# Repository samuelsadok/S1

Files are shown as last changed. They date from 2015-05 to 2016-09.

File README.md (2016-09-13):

# AppInstall Innovation Labs S1

The S1 project is a small pocket drone, controlled by your smartphone via Bluetooth.

## Project State

Until now, about 10 instances of a prototype were manufactured. The firmware was written to a point where the throttle could be controlled by an iOS App. However, since then, the PID-controller has never been properly tuned, so flight could not yet be demonstrated.

To allow for better understanding of the physical system, and ultimately enable autonomous controller calibration, the implementation of a software-in-the-loop simulator was started.

The desire to make the contol protocol and application more universal contributed to the inception of the AmbientOS project. Since then, no progress was made on the S1 project. It will be resumed once the AmbientOS framework is capable enough to carry the S1 control App.

## Hardware Overview

The most important hardware components on the S1 prototype 1 hardware are:
- an AVR ATXmega32E5 microcontroller, dedicated to flight control tasks ("flight controller")
- a CSR1010 bluetooth microcontroller, dedicated to bluetooth communication ("baseband processor")
- an InvenSense MPU6050 inertial sensor (connected to the flight controller)
- 4 MOSFETs used to control the motors (connected to the flight controller)

The two microcontrollers are connected through an I2C connection, where the baseband processor
is the master and the flight controller is the slave.

## Known Hardware Issues

Hardware bugs in the S1 prototype 1 hardware, to be solved in updated versions:

 - the power supply is not stable when the motors draw a lot of current (possibly solved using a large (330 µF) capacitor)
 - the motor drivers require a capacitor and a resistor to protect them from high currents (else they break after some time)
 - the LEDs (and motors?) must not be connected to BAT- as this prevents the device from switching off completely

## Folder Structure

| Folder | Purpose |
| --- | --- |
| baseband			| application specific files for the baseband controller firmware |
| baseband_bootloader		| application specific files for the baseband controller bootloader |
| flightcontroller		| application specific files for the flight controller firmware |
| flightcontroller_bootloader	| application specific files for the flight controller bootloader |
| factory_bootloader	 	| application specific files for the factory bootloader |
| asf *				| Atmel Software Framework (hardware abstraction for Atmel microcontrollers) |
| shared-c *			| C code shared by all firmware applications |
| shared-c# *			| C# code shared by all applications |
| schematics			| Altium Designer circuit schematics and PCB layout of the quadrocopter and base station  |

The folders marked with a star are git subtrees (i.e. they are git repositories themselves)

## Git Structure

[To be defined]

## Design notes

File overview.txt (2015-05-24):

BLUETOOTH TOPICS

service
characteristic
descriptor
attribute

ads
connection
pairing
bond
irk
	identity resolve key (max 1 per bond)
diversifier
	
white list
address types

HOW TO BOOTSTRAP AN EMPTY DEVICE

The flight processor flash can be accessed through the ISP connection. This way,
a factory bootloader code can be written to the device along with a I2C bootloader.
The factory bootloader will then program the baseband processor with its bootloader
so that the the device is available for over-the-air updates.

FLIGHT PROCESSOR BOOTLOADER

If magic number = 0xB007, control is transferred to the application
immediately without anychecks. This special case is only used for
factory bootstrapping.
If magic number = 0xB007, wait for a firmware update on I2C (connected
to the baseband) or for a command to launch the application.
If magic code != 0xC0DE, the bootloader refuses to launch the application.
When a firmware update begins, the magic number is invalidated.
After a firmware has been received and the checksum is valid, the magic number
is set to 0xC0DE.

FLIGHT PROCESSOR FACTORY BOOTLOADER

Contains the baseband bootloader hardcoded and uses software I2C to program
the onboard EEPROM. After programming and verifying the baseband bootloader,
the flight processor is put into DFU mode by invalidating the magic number.

FLIGHT PROCESSOR APPLICATION

Controls the flight systems and waits for control commands on I2C. If no commands
are received for a while, the motors are shut down. The application can be commanded
to transfer control to the bootloader.

BASEBAND BOOTLOADER

Tries to place the flight processor into bootloader mode.
If magic number = 0xC0DE and the bootloader reports that it has a valid application,
the DFU mode is only temporary and the bootloader disables itself, so that the next
reboot will start the application.
Sends advertisements using a "DFU mode" device name and exposes the DFU service.

BASEBAND APPLICATION

Tries to command the flight processor to enter application mode. If this fails, it
bugchecks. Any bug check in the application will temporarily put the device into to DFU mode.

DFU SERVICE (while in DFU mode)

DFU version			r
baseband version		r	may be unknown
baseband application		rw	Reading maps to the active application, writing maps to the inactive application and stages it for activation.
flight software version		r	May be unknown
flight processor application	rw	Writing to this locks the baseband processor (and consequently the flight processor) to DFU mode
state				rw	Reading from this indicates whether the DFU mode is temporary or permanent (locked).
					Writing to this causes both bootloaders to check their application and possibly activate it if valid. This will unlock the device from DFU mode.

DFU SERVICE (while in normal mode)

DFU version			r
state				rw	Reading from this indicates that the device is in normal mode.
					Writing to this causes the device to enter temporary DFU mode.

IMAGE FILE
proj.xuv contains what should be in the RAM

proj.flash.xuv and proj.img contain a mapping of the RAM:
All values are 16 bit values and are stored in EEPROM in little endian.

[Control Header]:
CRC of some kind (?)
number of blocks n (stored in EEPROM in big endian!)
SCL high/low period: 5050 on flash, 0F15 on EEPROM

[n Block Headers]:
byte offset in image
address in memory (in words)
byte length
CRC of the block contents

[n Data Blocks]

Code memory (program counter) maps to memory address 0x2000
After loading the image, the code starts at memroy address 0x2010 (code address 0x10)
at memory address 0x2008, we find 8 words of info for the firmware:
1 word: function pointer to the program entry point (ram_app_init)
6 words: firmware patch bitmap
1 word: pointer to the firmware patch table
the patch table consists of 24 (?) pairs of words:
- ??
- function pointer (to somewhere in the image)

CSR ABI:
if all arguments are 16bit wide:
1st arg: al
2nd arg: ah
3rd arg: y+0
4th arg: y+1
5th arg: y+2

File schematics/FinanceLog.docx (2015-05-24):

Item | Quantity | Amount
Apple iOS Developer Access (2014) | 1 | $100
Xamarin.iOS Business (2014) | 1 | $100
Motors (incl. shipping) | 100 | $120
Batteries (incl. shipping) | 2x 30 | $240
PCBs (incl. shipping) | 25+5 | $1500
Total | | $2060

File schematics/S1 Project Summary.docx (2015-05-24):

# S1 Project Overview

# The Product

Codename S1 designates a toy quadrocopter characterized by its small size and employment of a smartphone as a remote control. The device consists of one single PCB[^1] that also provides a frame for the motors and the battery. The device is shipped in a carrying case that at the same time acts as a mobile charging base. The charging base comes with its own rechargeable battery and can be charged on any USB port using the included Micro-USB cable. The estimated dimensions of the carrying case are 100x100x40mm.

All these factors should encourage the user to take the device wherever he goes.

To further enhance user experience, we consider including a replacement battery and replacement propellers in every package. We will also offer all replacement parts separately on our website.

The S1 is remote controlled via Bluetooth 4.0 Low Energy (aka Bluetooth Smart). This enables a wide range of potentially compatible devices, including iOS devices (2011 or newer), other smartphones and tablets with Bluetooth LE, Macintosh Laptops (2011 or newer) and Windows 8 Laptops. Another possibility is to build a Bluetooth dongle for a Sony PS4 controller to enable the most intuitive way of controlling the device. However, since we have very limited work forces, we fill initially focus solely on iOS devices.

# Technical Details

## Device

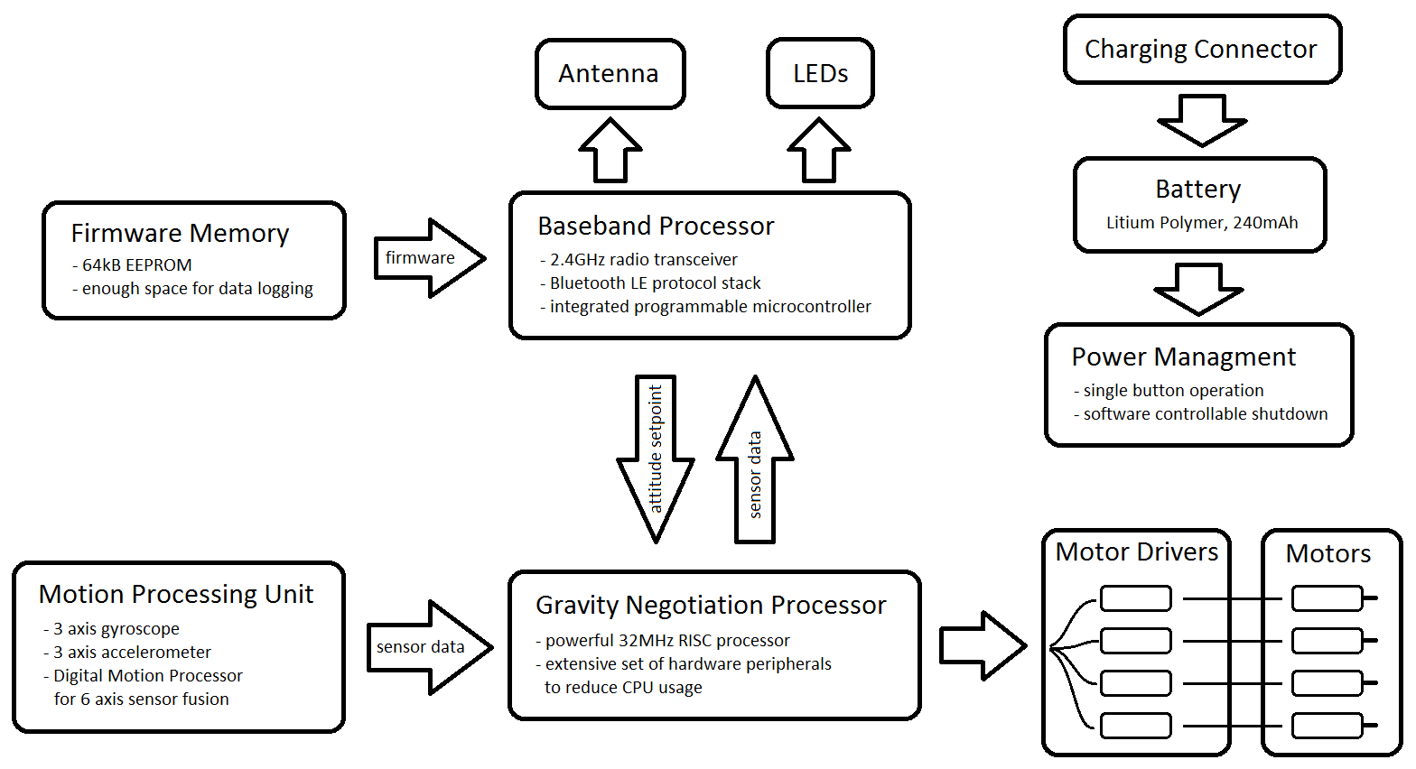
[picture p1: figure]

A quadrocopter is an inherently unstable flying machine and as such requires a closed high speed control loop to keep it airborne. The gravity negotiation processor makes this possible by implementing a Kalman Filter and a PID controller that maps the orientation angle to motor outputs. The Kalman Filter compensates for the lag between input and output while at the same time acting as a low pass filter. The PID controller mirrors the physical model of the quadrocopter and constantly tries to reduce the error between the measured orientation angle and the set orientation angle.

The motion processor takes away a lot of the mathematical complexity by implementing full 6 axis sensor fusion. It also provides special features such as high-G and zero-G detection that could be used to start the motors when the device is being dropped.

The baseband processor controls all communication with the remote control app on the smartphone. The chip comes with a comprehensive software framework and a wide range of sample code that will greatly simplify development.

## Base Station

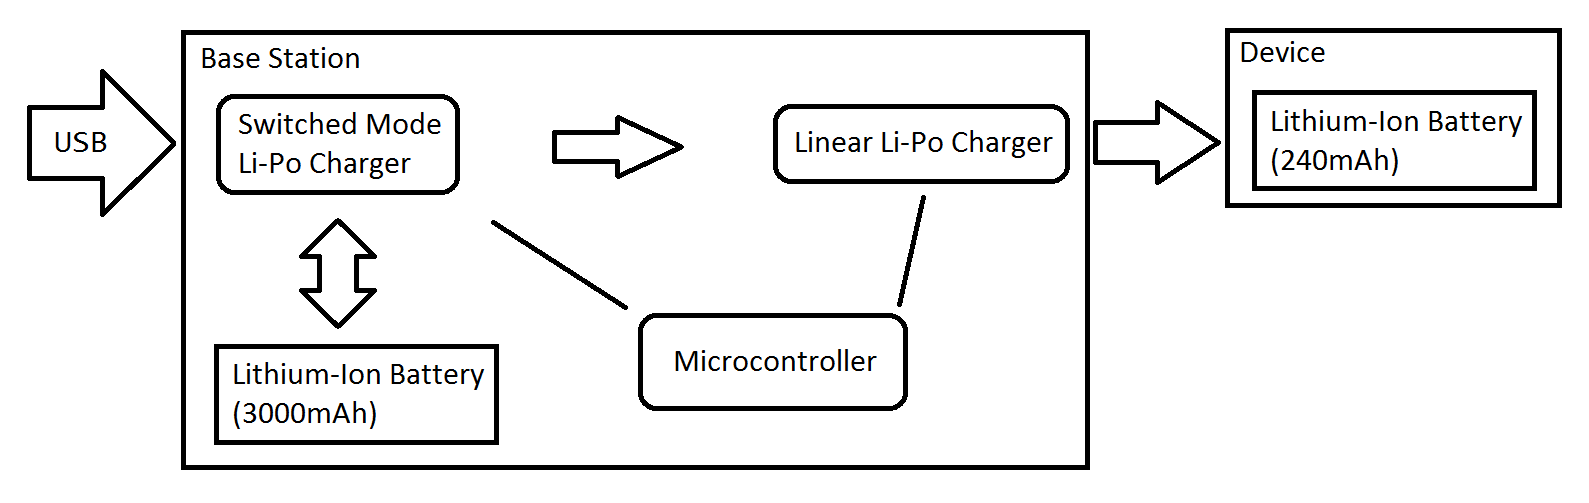
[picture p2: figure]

The base station battery is charged by a power management chip that is connected to the USB port. A switched mode charger is used to maximize efficiency and reduce heat dissipation. A USB interface chip requests maximum power from the USB port (500mA instead of 100mA) to accelerate charging. It can also detect if a wall plug is used instead of a USB data port, as a wall plug can provide up to 2A.

The second battery charger chip regulates charging of the target device. A linear mode regulator is used here to reduce system complexity.

A microcontroller is used to control and monitor the charging state of both chargers. A single tactile switch with an integrated dual color LED is used to switch the system on and off and display the charging state. The microcontroller will be fitted with a bootloader to enable firmware updates via USB.

# Current State

## Prototype

[pic]

Note that the release versions will look much cleaner. The wires on the device are only used to program and debug the firmware. They do in no way assist the device at run time.

For both components of the system (the device itself as well as the base station) we constructed a prototype to resolve various uncertainties. In both prototypes we found some issues that were fixed in the release design.

- The power switch is obscured by the propellers when switched on. We have replaced the switch by a simple button that is mounted at a right angle.
- The resistors for the motor drivers break easily due to mechanical stress on the arms
- It is hard to efficiently solder the motors. We have revised the way the motors are connected to the PCB. This way we also reduced the risk of damaging the copper tracks on the arms.
- The base station cannot reliably detect Apple wall plugs. This is suboptimal because charging times are much slower than they could be. The release design will enable the microcontroller to distinguish between power sources.
- The boost converter on the base station doesn’t work. Without this component, charging is only possible when the station is connected to USB. We’re still investigating this issue. A possible explanation is a soldering defect which would not be present in professionally assembled PCBs.

## Production

[pic]

We have already acquired 30 small batteries for the device, 30 large batteries for the base station, 100 motors and a limited number of propellers. All of these components are of great quality and meet our requirements. We are in contact with potential supplies of plastic parts, tin boxes and more propellers and have settled on a PCB fab and assembly house.

# What can go wrong

Some component doesn’t fit on its footprint on the PCB
This can be very well avoided by thoroughly checking all components against the respective datasheet. All components we use are well documented. Our chief engineer can also proudly present an absolutely clean record in terms of PCB footprint compliance of components.

The Bluetooth link doesn’t work
The chip we use for Bluetooth communication is very well documented and comes with a broad range of sample application source code as well as hardware designs. Our Bluetooth related part of the system is basically identical to these sample designs, which reduces the risk of a critical error almost to zero. Still, 2.45GHz is a high frequency and as such requires fine tuning of the Antenna circuit to maximize range. Since we don’t have the equipment do conduct HF measurements, range might be less than optimal.

Something else in hardware doesn’t work
The S1 hardware is generally quite simple compared to other designs, due to the fact that most features will be implemented in software. This reduces the number of potential errors. Also, a major portion of the design is proven to work reliably. Hence the probability of a generic hardware bug is negligible.

A software bug is found after release
No piece of code is completely bug free. Therefore we will implement a so called bootloader in all processors. A bootloader is a small application that is capable of loading code from some other source. The update system will be implemented in such a way that it provides a seamless experience for the end user. To release a new firmware, we will embed the firmware package in the iOS App and then publish the updated app. The updated app will detect that the S1 is running an old firmware and will then transmit the new firmware wirelessly without requiring user intervention.

# Potential Market

Looking at similar products, there is no doubt that there is a market for a micro toy quadrocopter, with a volume far greater than our initial batch of 30 pieces. To enforce this claim, we refer to the following products:

AR Drone by Parrot: http://ardrone2.parrot.com/ (>100’000 units sold)
HobbyKing Pocket Quad Ultra Micro DSM2: http://www.hobbyking.com/
Syma S107 (see Amazon)

There are countless other products in this market, but we have yet to find one that exactly matches the selling points of S1.

# Rollout

The S1 will be sold through the dedicated website http://innovation-labs.appinstall.ch/ for $99. Worldwide shipping costs are up to $20. The preferred payment method will be PayPal as it provides the user with security and is easy to incorporate into a website. A Youtube video will provide a means of making the product known to a wide audience. We are confident that once a small consumer base is established, it will continue to grow through word of mouth. Another possibility is to sell the product on Richardo, Ebay or any local RC shops.

After successful rollout, we will start selling replacement parts for the lowest price possible.

In order to win the interest of hobbyists the entire project will be open source.

# Investment Plan

The initial batch will be 30 units. A lower quantity is not feasible since there are significant fixed costs (shipping, tooling, minimum order quantities, etc.). Below is an overview of all costs that are associated with the project, divided into three groups. Not recognized are development costs.

## Past

These items are already at our office and have been paid for.

Item | Quantity | Amount
Apple iOS Developer Access | 1 | $100
Motors (incl. shipping) | 100 | $120
Batteries (incl. shipping) | 2x 30 | $240
Total | | $460

## Imminent

These items are required for the first S1 demonstration and need to be ordered as soon as possible.

Item | Quantity | Amount
PCB Tooling | once | $90
PCB Fabrication | 30 | $70
PCB Assembly | 30 | $300 (estimated)
Electrical Components | for 30 | $950 (estimated)
Total | | $1410

## Delayed

These items are required for release and can be ordered after successful demonstration of the S1.

Item | Quantity | Amount
Propellers (incl. shipping) | 100 | $90
Plastic Parts | 30 | $25 (best case)
Tin Boxes (incl. shipping) | 25 | $50
Total | | $165

What we’re requesting from our investors are partial funds for the “imminent” section. Our account balance is currently… oh wait, never mind. We just found out that our account balance is $1140 with $560 being added on 1st of January 2014. That means that we have sufficient funds to finance the entire enterprise. Still, we ask our investors to stand by in case the costs increase unexpectedly.

# Future Plans

- Security: Software updates enable us to implement password protection to prevent theft. As long as there are very few devices, cyber security is not an issue. However, as this number grows, so does the number of potential threads. A code signature check can be implemented to prevent injection of malicious code which could easily render the device permanently unusable. A balance must be found between openness to developers and protection against hackers.
- Data Logging: since the device is remote controlled by a smartphone, it is a logical step to collect full flight data and other statistics (such as battery level and device health) from all users. This provides us with valuable insight on how the device can be improved. It would also enable the end user to review his flights online. For the sake of privacy, the user must be able to disable logging.
- In the near future we will start experimenting with inductive coupling for wireless charging. If it turns out to be feasible, we will implement this technology in the next hardware generation.

[^1] A PCB (Printed Circuit Board) is a board on which all electrical components are soldered. The board holds two or more layers of copper tracks that interconnect the components.

AppInstall Innovation Labs CONFIDENTIAL 22.12.2013

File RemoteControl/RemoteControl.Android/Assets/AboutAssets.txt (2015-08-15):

Any raw assets you want to be deployed with your application can be placed in
this directory (and child directories) and given a Build Action of "AndroidAsset".

These files will be deployed with you package and will be accessible using Android's
AssetManager, like this:

public class ReadAsset : Activity
{
	protected override void OnCreate (Bundle bundle)
	{
		base.OnCreate (bundle);

		InputStream input = Assets.Open ("my_asset.txt");
	}
}

Additionally, some Android functions will automatically load asset files:

Typeface tf = Typeface.CreateFromAsset (Context.Assets, "fonts/samplefont.ttf");

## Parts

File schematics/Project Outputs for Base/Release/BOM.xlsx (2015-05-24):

Name | Manufacturer | Description | Designator | Footprint | Quantity
Cap 100nF |  | Ceramic Capacitor 100nF | C1, C5, C16, C17 | 0201 | 4
Cap 4.7µF |  | Ceramic Capacitor 4.7µF | C2, C13, C18, C19 | 0402 | 4
Cap 47pF |  | Ceramic Capacitor 47pF | C3, C4 | 0201 | 2
Cap 1µF |  | Ceramic Capacitor 1µF | C6, C7, C11, C14, C15 | 0201 | 5
Cap 2.2µF |  | Ceramic Capacitor 2.2µF | C8, C12 | 0402 | 2
Cap 33nF |  | Ceramic Capacitor 33nF | C9 | 0201 | 1
Cap 22µF |  | Ceramic Capacitor 22µF | C10 | 0805 | 1
Res 27R |  | Resistor 27R | R1, R2 | 0201 | 2
Res 100R |  | Resistor 100R | R3 | 0201 | 1
Res 10k |  | Resistor 10k | R4, R5, R10, R11 | 0201 | 4
Res 4k7 |  | Resistor 4k7 | R7, R8 | 0201 | 2
Res 2k2 |  | Resistor 2k2 | R9 | 0201 | 1
AP7313-33SA | Diodes Inc. (alternatives may be available) | Low Dropout Regulator 3.3V, 150mA | A1 | SOT23 | 1
1051330001 | Molex Inc. | Micro USB Type B Receptacle | J1 | special | 1
IFSC1008ABER1R0M01 | Vishay Dale (alternatives may be available) | Inductor 1µH | L1, L2 | 2x2.5mm Inductor | 2
ATXmega32E5 | Atmel | 8-Bit AVR Microcontroller | U1 | QFN-32 (5x5mm) | 1
FT230X | FTDI Ltd. | USB-UART Bridge | U2 | QFN-16 (4x4mm) | 1
bq24250 | Texas Instruments | LiPo Chargering Regulator with Step-Down Converter | U3 | QFN-24 (4x4mm) | 1
FAN4860UMP5X | Fairchild Semiconductor | Boost Converter 5V | U4 | 6-UMLP | 1
MCP73831T-2ATI | Microchip Technology | 500mA Linear LiPo Charger | U5 | SOT-23-5 | 1
BAS16SL | Fairchild Semiconductor (alternatives my be available) | Diode | V1 | SOD923 | 1
 |  |  |  | Total: | 39
all capacitors should be 10V or more
all resistors should be 1%
S1 and J2 should not be assembled

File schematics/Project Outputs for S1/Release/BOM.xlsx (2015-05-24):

Name | Manufacturer | Description | Designator | Footprint | Quantity
Cap 1µF |  | Ceramic Capacitor 1µF | C1, C2 | 0201 | 2
Cap 2.2nF |  | Ceramic Capacitor 2.2nF | C8 | 0201 | 1
Cap 2.2µF |  | Ceramic Capacitor 2.2µF | C16, C20 | 0402 | 2
Cap 8.2pF |  | Ceramic Capacitor 8.2pF | C12 | 0201 | 1
Cap 15pF |  | Ceramic Capacitor 15pF | C11 | 0201 | 1
Cap 33pF |  | Ceramic Capacitor 33pF | C17 | 0201 | 1
Cap 47nF |  | Ceramic Capacitor 47nF | C15, C21 | 0201 | 2
Cap 47µF |  | Ceramic Capacitor 47µF | C18 | 0805 | 1
Cap 100nF |  | Ceramic Capacitor 100nF | C3, C4, C5, C6, C7, C9 | 0201 | 6
Cap 150nF |  | Ceramic Capacitor 150nF | C14 | 0201 | 1
Cap 470nF |  | Ceramic Capacitor 470nF | C10, C13, C19 | 0201 | 3
Res 4k7 |  | Resistor 4k7 | R7, R8, R9, R10 | 0201 | 4
Res 10k |  | Resistor 10k | R1, R2, R3, R4 | 0201 | 4
Res 100R |  | Resistor 100R | R5, R6 | 0201 | 2
8Y-16.000MAAV-T | TXC Corp. (alternatives may be available) | Crystal 16MHz | X2 | Crystal 1.6mm x 2mm | 1
ABS05-32.768KHZ-9-T | Abracon Corp. (alternatives may be available) | Crystal 32.768kHz | X3 | Crystal 1mm x 1.6mm | 1
AP7333-28SAG | Diodes Inc. (alternatives may be available) | Low Dropout Regulator 2.8V, 300mA | A1 | SOT23 | 1
AT24C512C | Atmel | 512kbit I2C EEPROM | U4 | UDFN-8 (3x2mm) | 1
ATXmega32E5 | Atmel | 8-Bit AVR Microcontroller | U1 | QFN-32 (5x5mm) | 1
BAS16SL | Fairchild Semiconductor (alternatives my be available) | Diode | V6 | SOD923 | 1
CSR1010 | Cambridge Silicon Radio | Bluetooth v4.0 Low Energy Chip | U3 | QFN-32 (5x5mm) | 1
DMG2302U | Diodes Inc. (alternatives may be available) | MOSFET N-Channel | V1, V2, V3, V4, V5 | SOT23 | 5
MLZ1608E4R7M | TDK Corp. | Inductor 4.7µH | L1 | 0603 | 1
LNJ352W83RA | Panasonic | Side View LED | H1, H2 | special | 2
MPU6050 | Invensense | 9DOF Motion Processing Unit | U2 | LQFN24 (4x4mm) | 1
0781710004 | Molex Inc. | Programming & Charging Connector for S1 | J1 | special | 1
TL1014BF160QG | E-Switch | Tactile Switch, Right Angle | S1 | special | 1
W3008 | Pulse Electronics Corp. | Antenna 2.4GHz | X1 | special | 1
 |  |  |  | Total | 50
all capacitors should be 10V or more
all resistors should be 1%

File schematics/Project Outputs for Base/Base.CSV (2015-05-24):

Comment | Description | Designator | Footprint | Quantity
AP7313-33SA | Low Dropout Regulator 3.3V, 150mA | A1 | SOT23 | 1
Cap 100nF | Ceramic Capacitor 100nF | C1, C5, C16, C17 | 0201 (C) | 4
Cap 4.7µF | Ceramic Capacitor 4.7µF | C2, C13, C18, C19 | 0402 (C) | 4
Cap 47pF | Ceramic Capacitor 47pF | C3, C4 | 0201 (C) | 2
Cap 1µF | Ceramic Capacitor 1µF | C6, C7, C11, C14, C15 | 0201 (C) | 5
Cap 2.2µF | Ceramic Capacitor 2.2µF | C8, C12 | 0402 (C) | 2
Cap 33nF | Ceramic Capacitor 33nF | C9 | 0201 (C) | 1
Cap 22µF | Ceramic Capacitor 22µF | C10 | 0805 (C) | 1
USB | Micro USB Type B Receptacle | J1 | MICRO USB RECEPTACLE VERTICAL | 1
Battery | Connector 2-Pos 2.54mm Pitch | J2 | Conn 2-Pos 2.54mm Pitch | 1
L 1µH | Inductor 1µH | L1, L2 | INDUCTOR 2X2.5MM | 2
Res 27R | Resistor 27R | R1, R2 | 0201 (R) | 2
Res 100R | Resistor 100R | R3 | 0201 (R) | 1
Res 10k | Resistor 10k | R4, R5, R10, R11 | 0201 (R) | 4
Res 4k7 | Resistor 4k7 | R7, R8 | 0201 (R) | 2
Res 2k2 | Resistor 2k2 | R9 | 0201 (R) | 1
ITS13FV1 | Through-Hole Tactile Switch | S1 | SWITCH THROUGH-HOLE | 1
Xmega32E5 | 8-Bit AVR Microcontroller | U1 | QFN-32 (5X5MM) | 1
FT230X | USB-UART Bridge | U2 | QFN-16 (4X4MM) | 1
bq24250 | LiPo Chargering Regulator with Step-Down Converter | U3 | QFN-24 (4X4MM) | 1
FAN4860UMP5X | Boost Converter 5V | U4 | 6-UMLP | 1
MCP73831 | 500mA Linear LiPo Charger | U5 | SOT-23-5 | 1
1N4148W | Diode | V1 | SOD923 | 1

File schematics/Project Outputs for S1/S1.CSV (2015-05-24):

Bill of Material for
On 03.01.2014 at 10:49:32
Comment | Pattern | Quantity | Components
1N4148W | SOD923 | 1 | V6 | Diode
8Y-16.000MAAV-T | CRYSTAL 1.6MM X 2MM | 1 | X2 | Crystal 16MHz
ABS05-32.768KHZ-9-T | CRYSTAL 1MM X 1.6MM | 1 | X3 | Crystal 32.768kHz
AP7333-28SA | SOT23 | 1 | A1 | Low Dropout Regulator 2.8V, 300mA
AT24C512C | UDFN-8 (3X2MM) | 1 | U4 | 512kbit I2C EEPROM
Cap 1µF | 0201 (C) | 2 | C1, C2 | Ceramic Capacitor 1µF
Cap 100nF | 0201 (C) | 6 | C3, C4, C5, C6, C7, C9 | Ceramic Capacitor 100nF
Cap 150nF | 0201 (C) | 1 | C14 | Ceramic Capacitor 150nF
Cap 15pF | 0201 (C) | 1 | C11 | Ceramic Capacitor 15pF
Cap 2.2µF | 0402 (C) | 2 | C16, C20 | Ceramic Capacitor 2.2µF
Cap 2.2nF | 0201 (C) | 1 | C8 | Ceramic Capacitor 2.2nF
Cap 33pF | 0201 (C) | 1 | C17 | Ceramic Capacitor 33pF
Cap 47µF | 0805 (C) | 1 | C18 | Ceramic Capacitor 47µF
Cap 470nF | 0201 (C) | 3 | C10, C13, C19 | Ceramic Capacitor 470nF
Cap 47nF | 0201 (C) | 2 | C15, C21 | Ceramic Capacitor 47nF
Cap 8.2pF | 0201 (C) | 1 | C12 | Ceramic Capacitor 8.2pF
CSR1010 | QFN-32 (5X5MM) | 1 | U3 | Bluetooth v4.0 Low Energy Chip
DMG2302U | SOT23 | 5 | V1, V2, V3, V4, V5 | MOSFET N-Channel
L 4.7µH | 0603 (L) | 1 | L1 | Inductor 4.7µH
LED1 | KLTFSN2K5200 | 2 | H1, H2 | Side View LED
MPU6050 | LQFN24 (4x4mm) | 1 | U2 | 9DOF Motion Processing Unit
Pico-EZMate | PICO-EZMATE (4PIN) | 1 | J1 | Programming & Charging Connector for S1
Res 100R | 0201 (R) | 2 | R5, R6 | Resistor 100R
Res 10k | 0201 (R) | 4 | R1, R2, R3, R4 | Resistor 10k
Res 4k7 | 0201 (C) | 4 | R7, R8, R9, R10 | Resistor 4k7
TL1014BF160QG | SWITCH RIGHT ANGLE | 1 | S1 | Tactile Switch, Right Angle
W3008 | ANTENNA 3.2X1.6MM (W3008) | 1 | X1 | Antenna 2.4GHz
Xmega32E5 | QFN-32 (5X5MM) | 1 | U1 | 8-Bit AVR Microcontroller

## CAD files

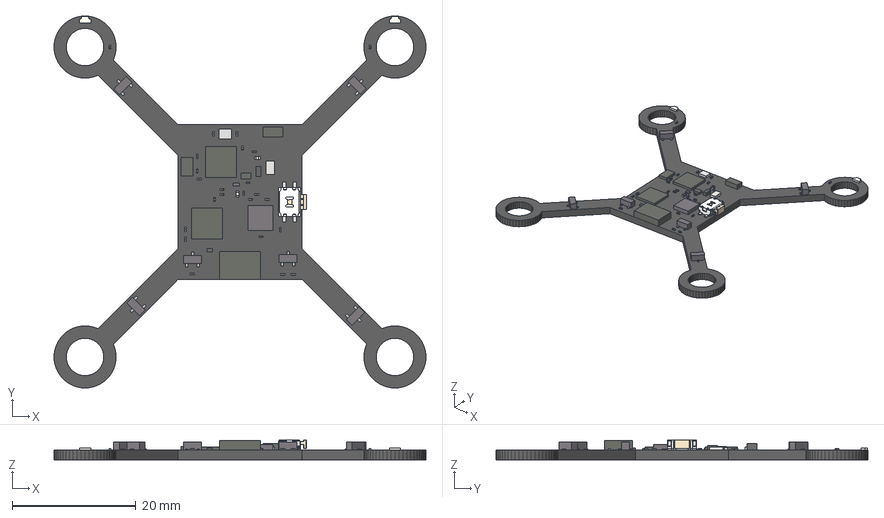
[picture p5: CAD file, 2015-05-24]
schematics/Project Outputs for S1/ExportSTEP/S1.step
60.0 x 60.0 x 3.22 mm
Board
Extruded x 116
TL1014_B_Housing
TL1014_Actuator
TL1014_Cover

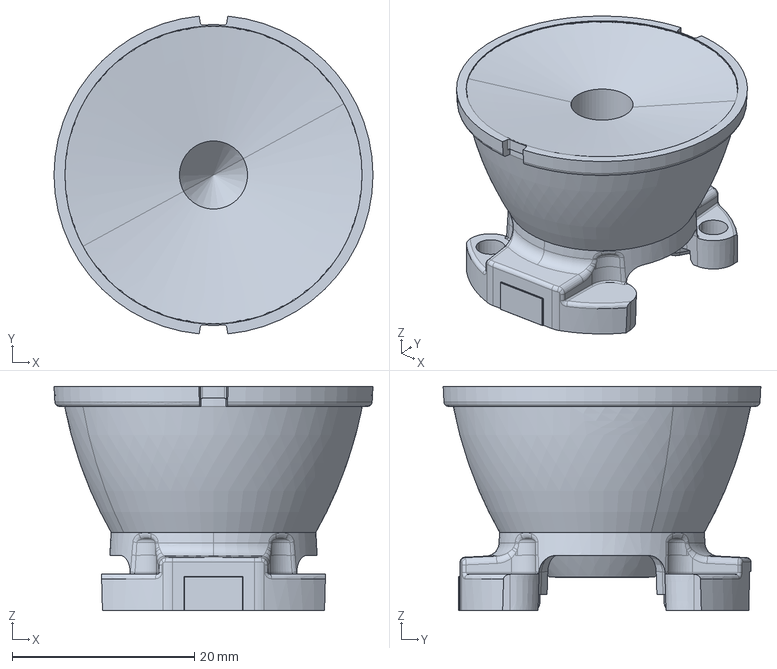
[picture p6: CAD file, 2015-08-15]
usbmodule/Models/20081114_pv_ledilstar_L_mechModel.stp
35.0 x 34.9 x 24.6 mm

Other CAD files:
schematics/CAD/S1_PCB.prt
schematics/Project Outputs for S1/ExportSTEP/416636384.prt
schematics/Project Outputs for S1/ExportSTEP/416638432.prt
schematics/Project Outputs for S1/ExportSTEP/416638560.prt
schematics/Project Outputs for S1/ExportSTEP/416638688.prt
schematics/Project Outputs for S1/ExportSTEP/416638944.prt
schematics/Project Outputs for S1/ExportSTEP/416639072.prt
schematics/Project Outputs for S1/ExportSTEP/416639200.prt
schematics/Project Outputs for S1/ExportSTEP/446768432.prt
schematics/Project Outputs for S1/ExportSTEP/446769328.prt
schematics/Project Outputs for S1/ExportSTEP/446769456.prt
schematics/Project Outputs for S1/ExportSTEP/446769584.prt
schematics/Project Outputs for S1/ExportSTEP/446769712.prt
schematics/Project Outputs for S1/ExportSTEP/446769840.prt
schematics/Project Outputs for S1/ExportSTEP/446770096.prt
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

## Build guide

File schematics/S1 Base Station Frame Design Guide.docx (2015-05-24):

# S1 Base Station Frame Design Guide

# Overview

The frame is the interface between four separate components.

- the S1 quadrocopter (located on top of the frame / embraced by the frame)
- the charging station PCB (located beneath the frame)
- the charging station battery (located beneath the quadrocopter and charging station PCB)
- the outer case

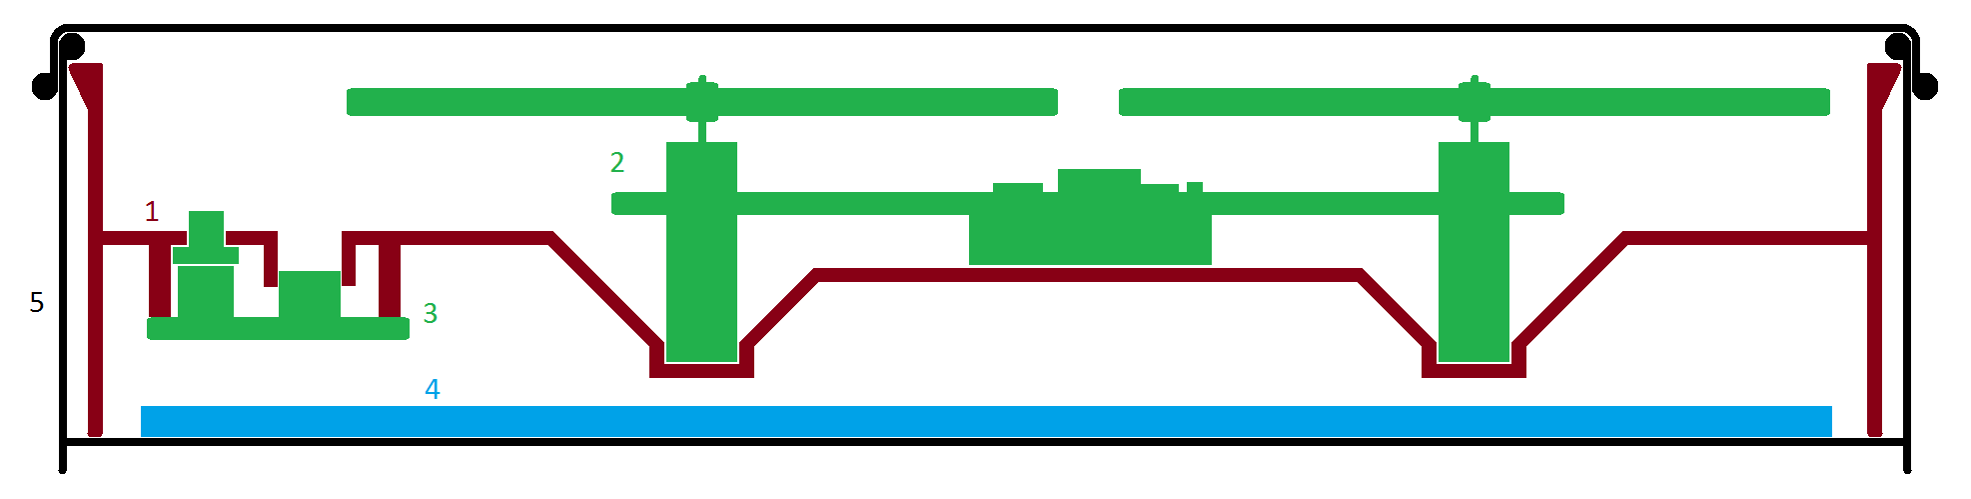
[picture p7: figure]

Sketch (side view) of the frame (1), quadrocopter (2), charging station PCB (3), charging station battery (4) and the case (5) – note that this sketch does not properly represent the relative sizes of the components (e.g. the charging PCB is much larger and will therefore reach far into the domain of the quadrocopter)

The strength of the frame shall be 1mm (uniformly).

The frame will be produced by joining two metal molds and filling them with two liquid plastic components. This means that no overhanging features on either side are allowed.

The overall appearance of the frame can be chosen at free will, as can any attributes that are not constrained by any of the four components.

3D CAD files of the quadrocopter and the charger PCB are available. Please contact the electrical engineering department for details.

# Quadrocopter

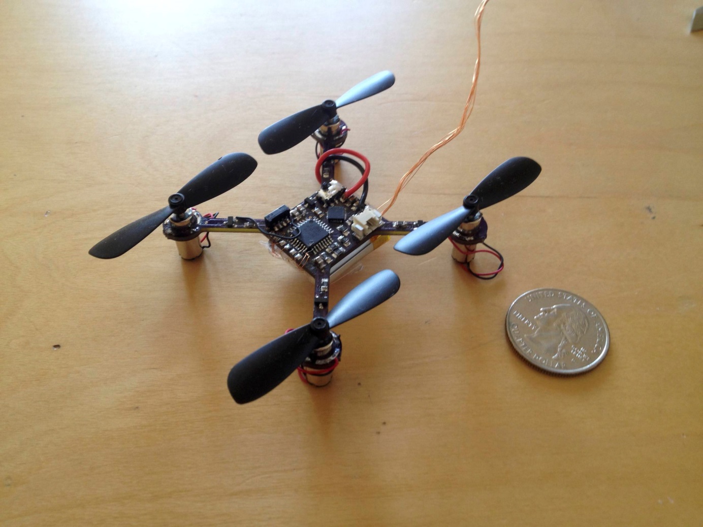
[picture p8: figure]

S1 Prototype – the physical shape of the release version will remain the same

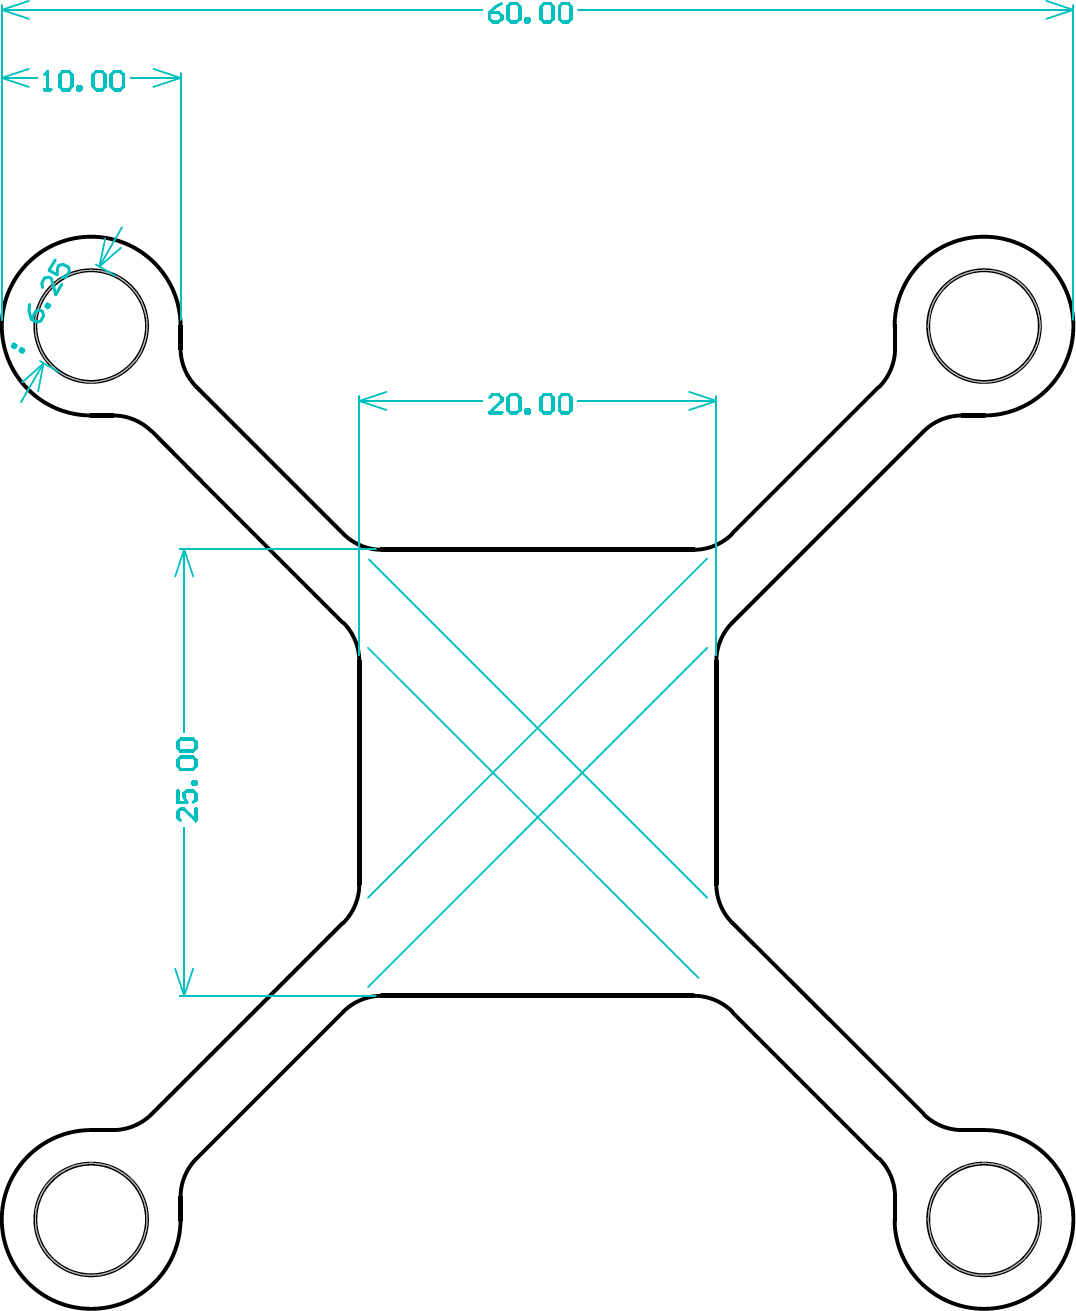
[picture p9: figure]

Outline of the quadrocopter PCB (all dimensions in mm)

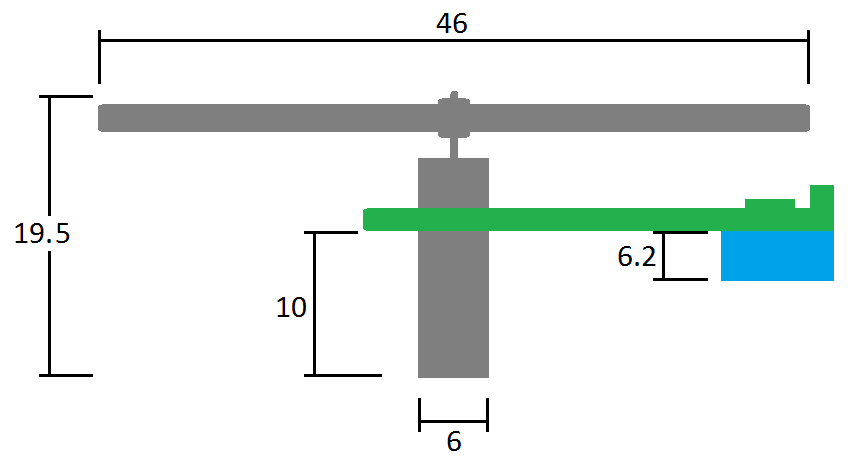
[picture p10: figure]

Sketch (side/front view) of one quadrocopter arm (all dimensions in mm) – the propellers can be assumed not to be wider than 10mm

The frame profile should be designed such that it touches the belly (the battery) of the quadrocopter. In this area the plastic strength should be decreased to 0.5mm in order to enable future extensions related to wireless charging.

A means has to be found to hold the quadrocopter in place for transport. A possible solution is to stretch a rubber band between two hooks drilled into the frame on either side of the quadrocopter.

# Charging Station PCB

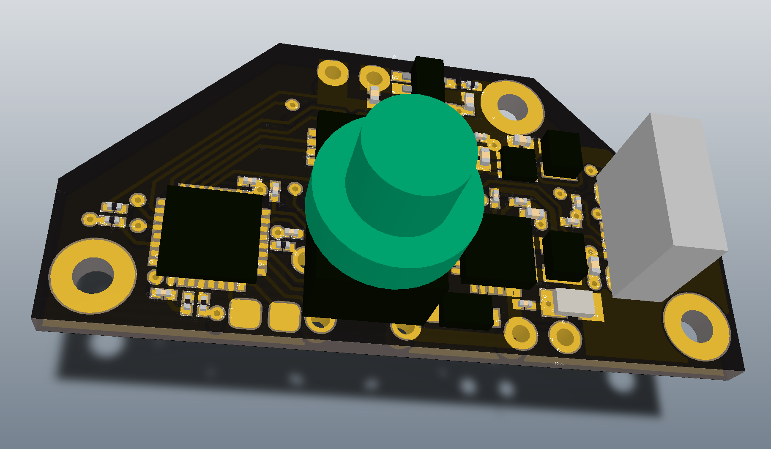
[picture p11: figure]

Preliminary 3D render of the charger PCB

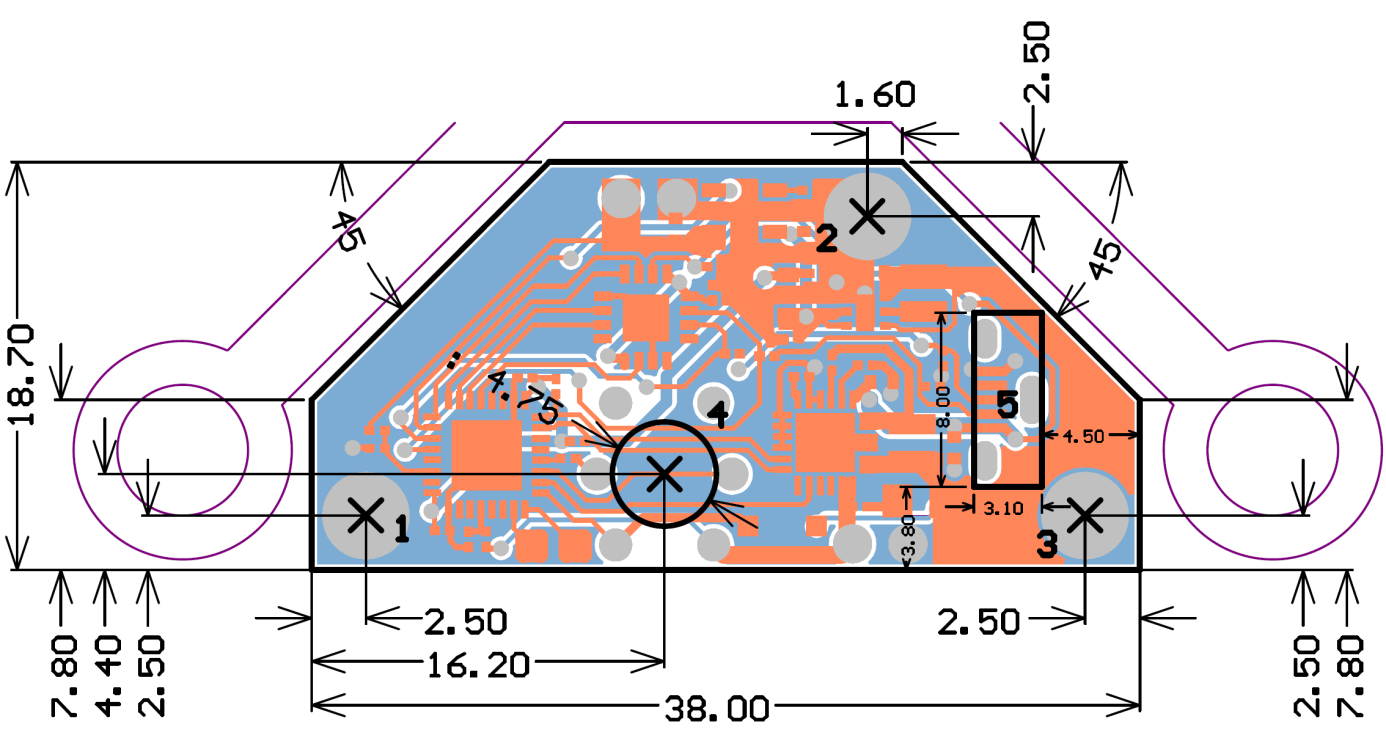
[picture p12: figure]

Top view of the charger PCB showing the positions of the screw holes (1-3), the power button (4) and the USB receptacle (5) (all dimensions in mm, angles in degrees)

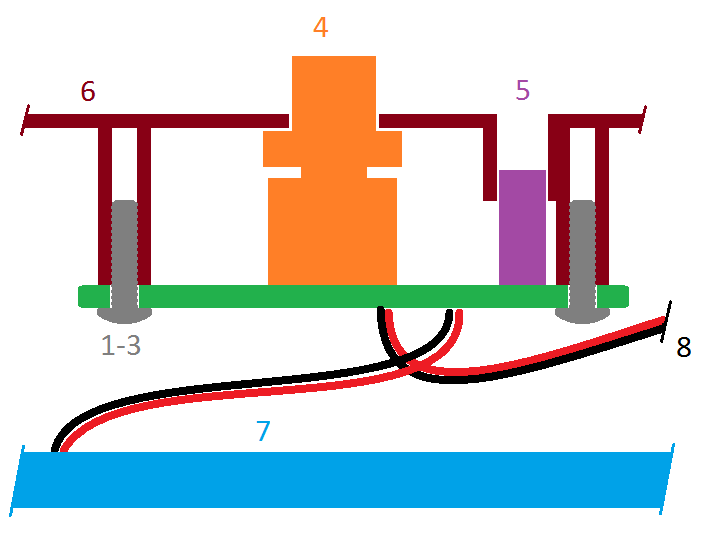
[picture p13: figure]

Front view of the charger PCB mounted to the frame (1-3: screws, 4: power button, 5: USB receptacle, 6: frame, 7: battery, 8: quadrocopter charging cable)

The frame will act as the front panel of the charger and as such shall incorporate a circular cutout for the power button (4) and a rectangular one for the vertically mounted Micro USB receptacle (5). The USB receptacle does not reach up to the frame so a channel-like structure could be considered to embrace the receptacle. Such a structure must not extend down for more than 4mm. The PCB is mounted to the frame using three M2 screws (1, 2 and 3). A 1.8mm drill hole is proposed. The diameter of the screw mounts shall not exceed 4mm. The gap between the PCB and the frame shall be 8mm. The PCB thickness is expected to be 1.6mm. The clearance beneath the PCB must be 7mm or greater to leave room for the battery connector.

A 3mm hole for the device charging cable must be placed somewhere in the frame. The location of this hole can be chosen freely as the harness is long enough.

# Charging Station Battery

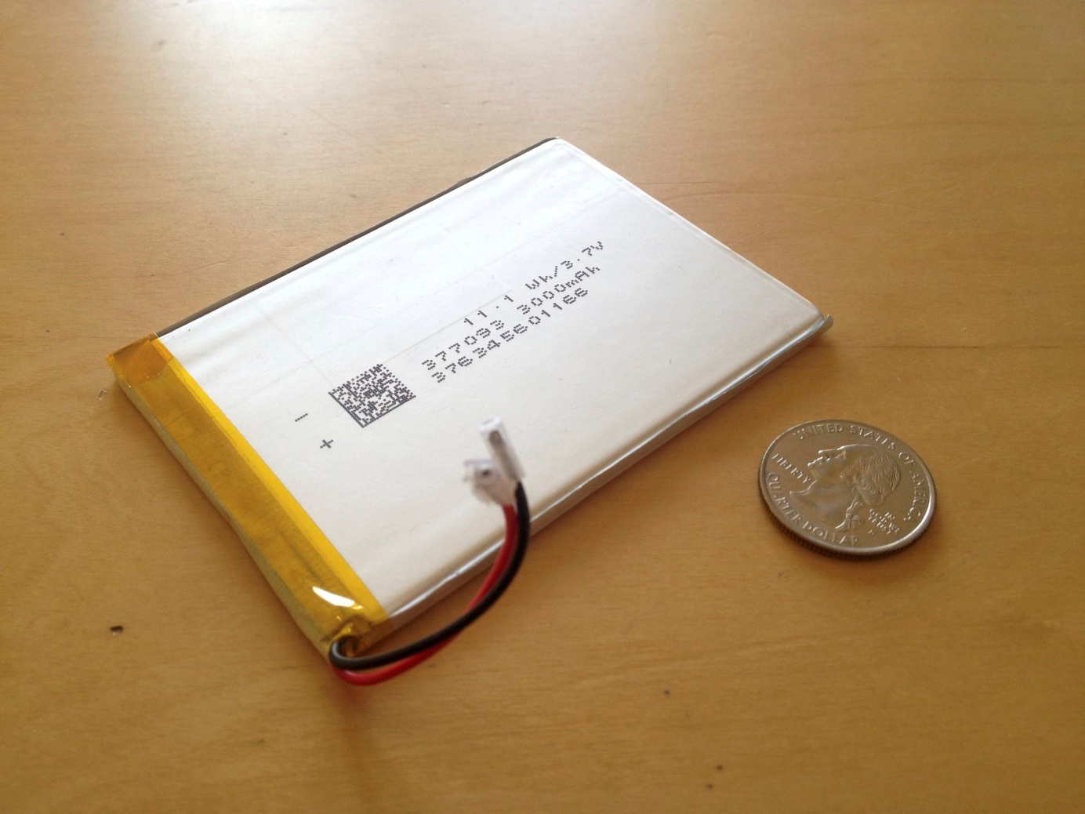
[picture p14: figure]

The charging station battery

The battery is the lowest component in the device and is attached directly to the bottom of the case using double sided tape. Its nominal dimensions are: 3.7*70*93mm. The frame shall not touch the battery but rather stand on a margin that is aligned with the border of the case.

# Outer Case

The case consists of a rectangular tin box with rounded edges. We are still looking for an adequate supplier, so the dimensions are not yet exactly known and should therefore be parameterized. For reference please use the inner dimensions 102mm*68mm*26mm with a corner radius of 10mm.

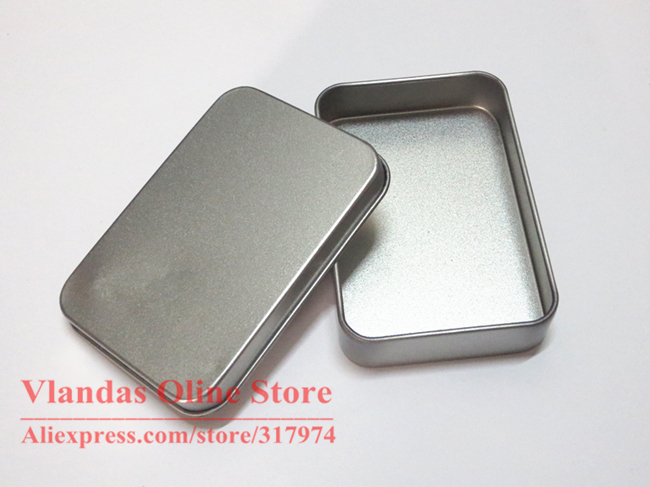
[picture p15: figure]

Tin box to be used as case

The upper edge of the case border extends slightly inwards. This leaves the opportunity for incorporating a clip that holds the frame in place. The preferred locations for such clips are the four corners.

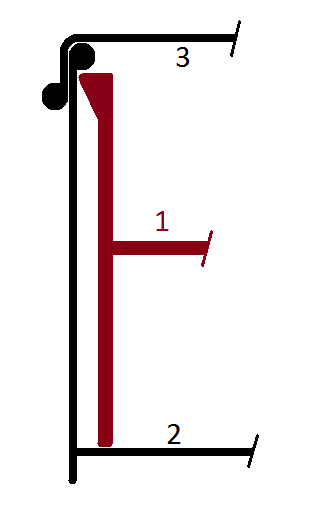
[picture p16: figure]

Sketch of the clip showing the frame (1), the tin box (2) and the lid (3)

consider the environment before printing this document

AppInstall Innovation Labs CONFIDENTIAL 31.12.2013

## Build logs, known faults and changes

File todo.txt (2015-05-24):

set mpu struct
mpu data format
init uav
--
i2c async read
i2c slave
i2c error handling
endpoints (control, configuration, version, logging)
unify i2c endpoints with bluetooth endpoints
extract factory bootloader
i2c bootloader (with 5s button)
nvm
DFU endpoint
i2c logging
power, battery, temperature
interrupt vectors at startup
bootloader range check
bug check
atomic
extract XUV
pack firmware

DFU service
i2c bootloader interface
config service
control service
state service

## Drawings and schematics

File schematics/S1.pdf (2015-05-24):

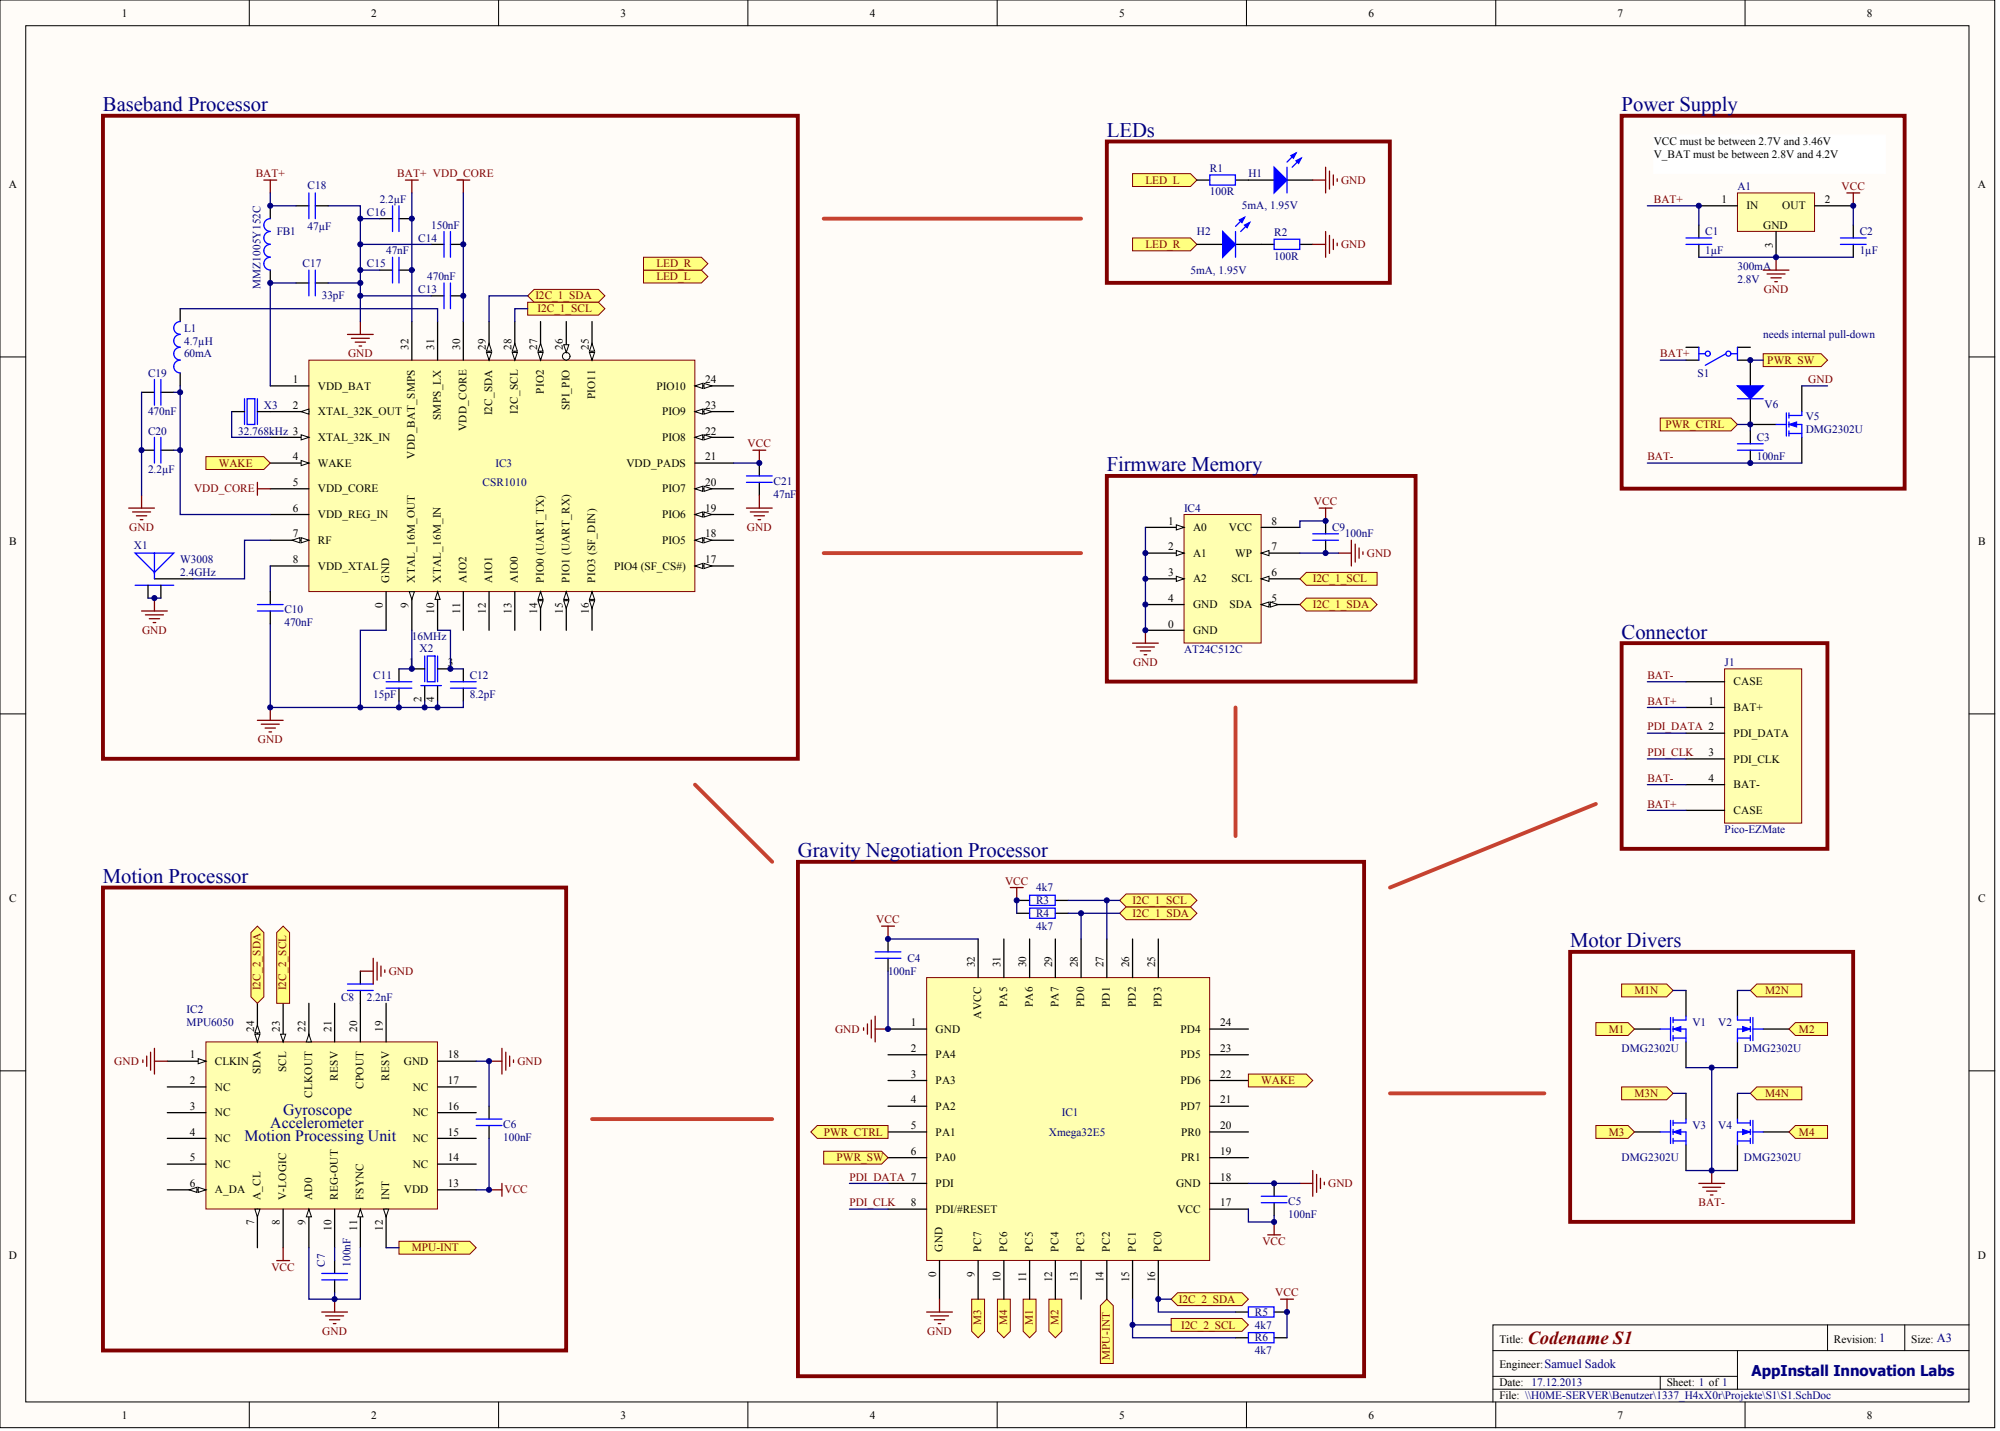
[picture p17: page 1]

VCC must be between 2.7V and 3.46V
V_BAT must be between 2.8V and 4.2V

needs internal pull-down

XTAL_32K_OUT 2

32.768kHz | XTAL_32K_IN 3

Codename S1 Title: | Revision: 1 | Size: A3

Engineer:Samuel Sadok | AppInstall Innovation Labs
Date: 17.12.2013 | Sheet: 1 of 1

\\H0ME-SERVER\Benutzer\1337_H4xX0r\Projekte\S1\S1.SchDoc
File:

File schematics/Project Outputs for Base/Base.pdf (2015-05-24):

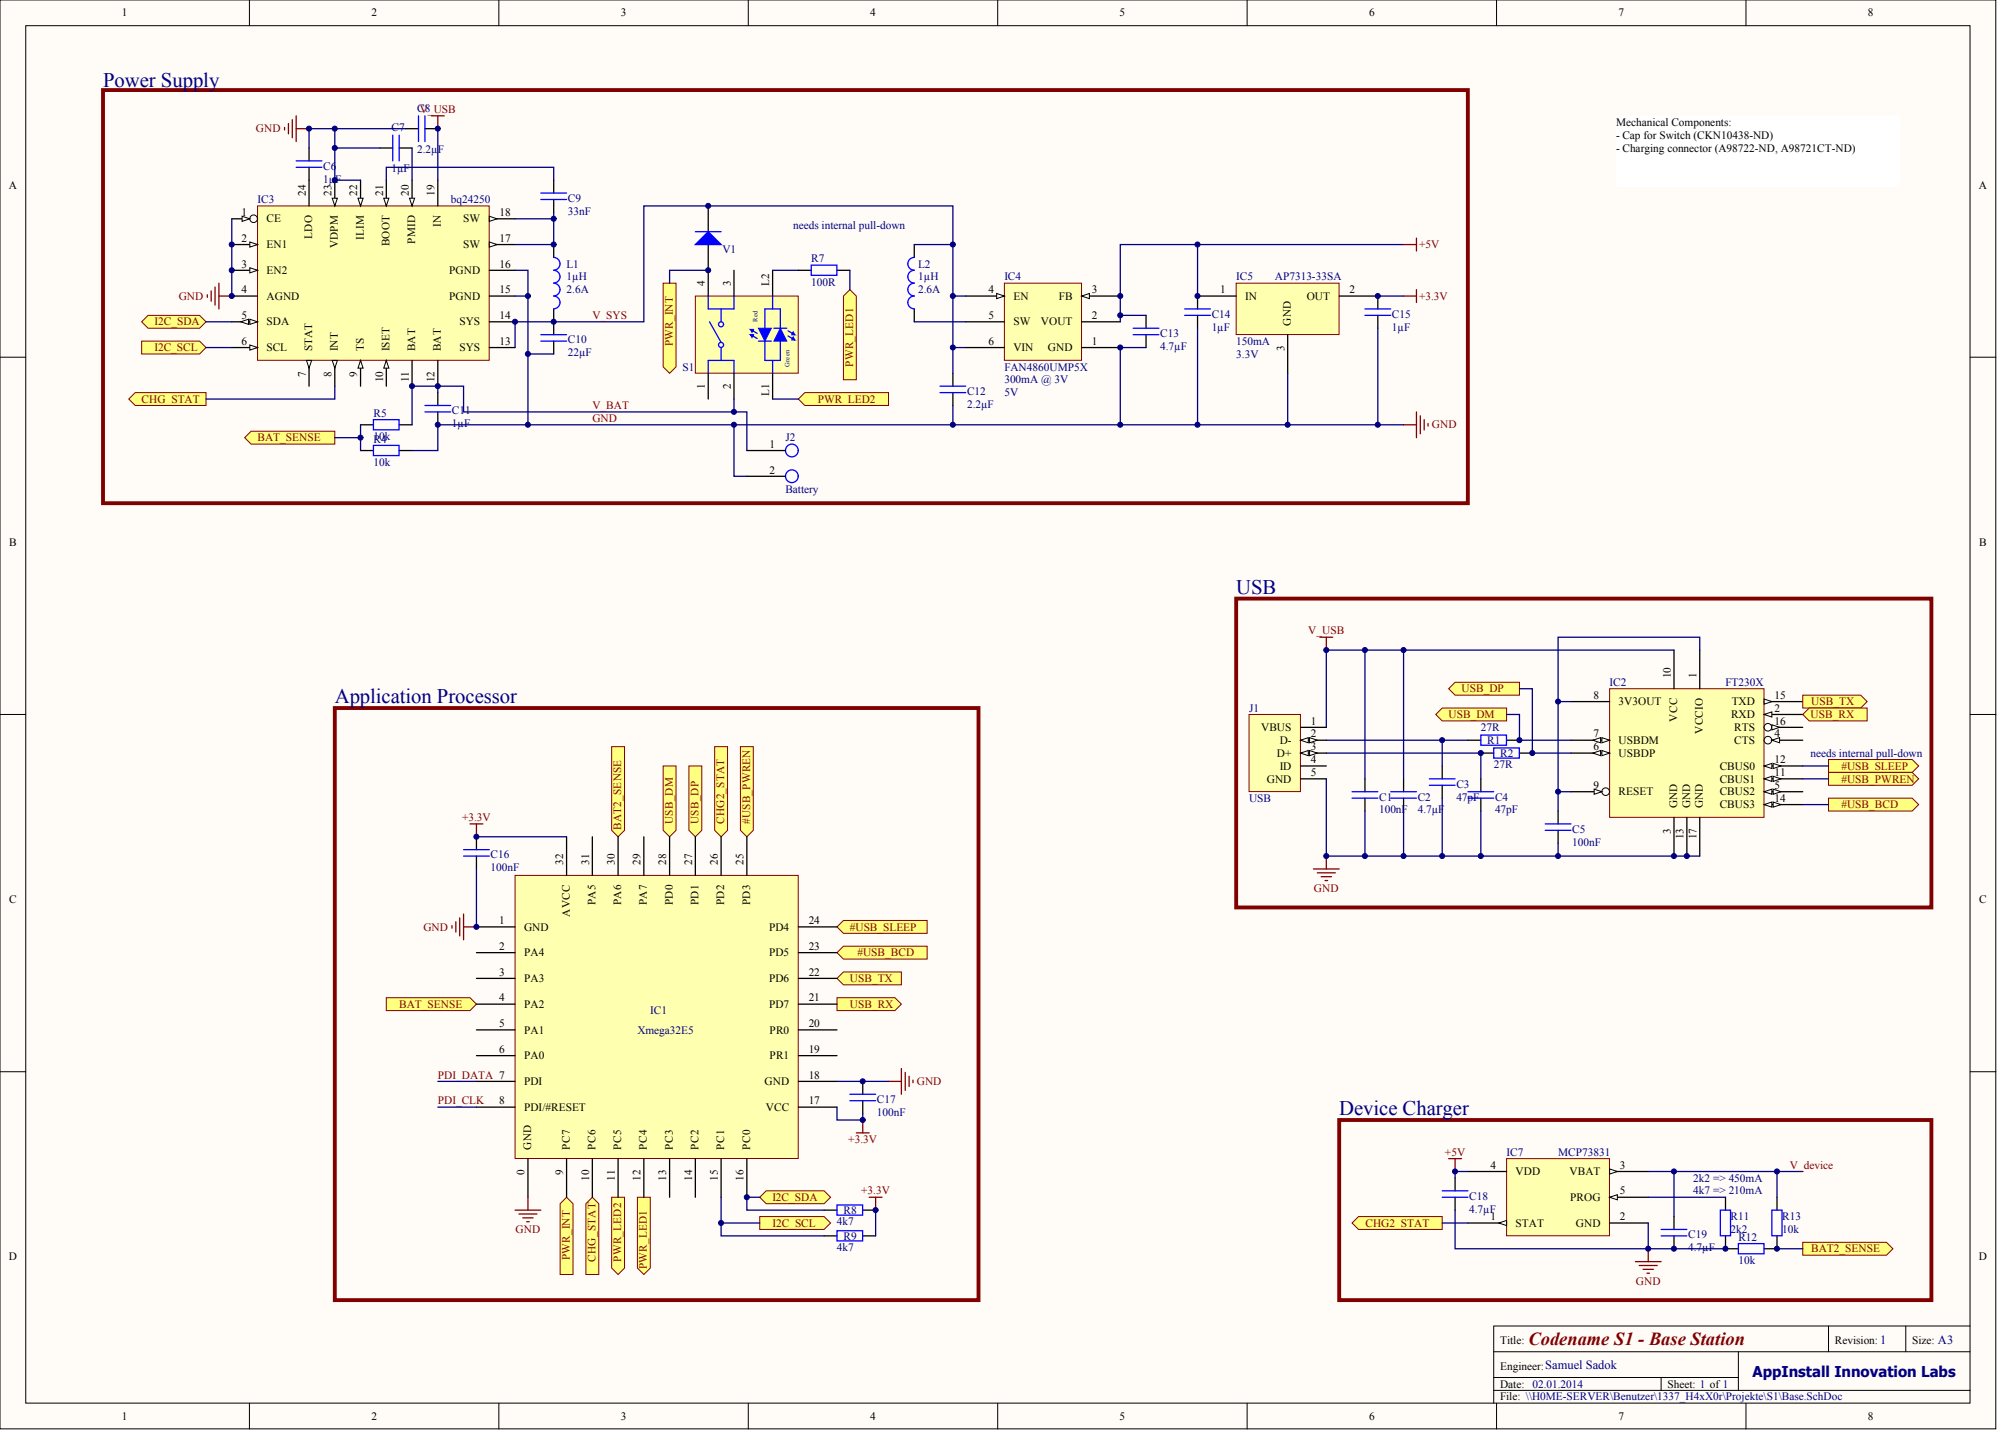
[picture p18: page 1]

Mechanical Components:
- Cap for Switch (CKN10438-ND)
- Charging connector (A98722-ND, A98721CT-ND)

needs internal pull-down

GND

Codename S1 - Base Station Title: | 1 Revision: | Size: A3

Engineer:Samuel Sadok | AppInstall Innovation Labs
Date: 02.01.2014 | Sheet: 1 of 1

\\H0ME-SERVER\Benutzer\1337_H4xX0r\Projekte\S1\Base.SchDoc
File:

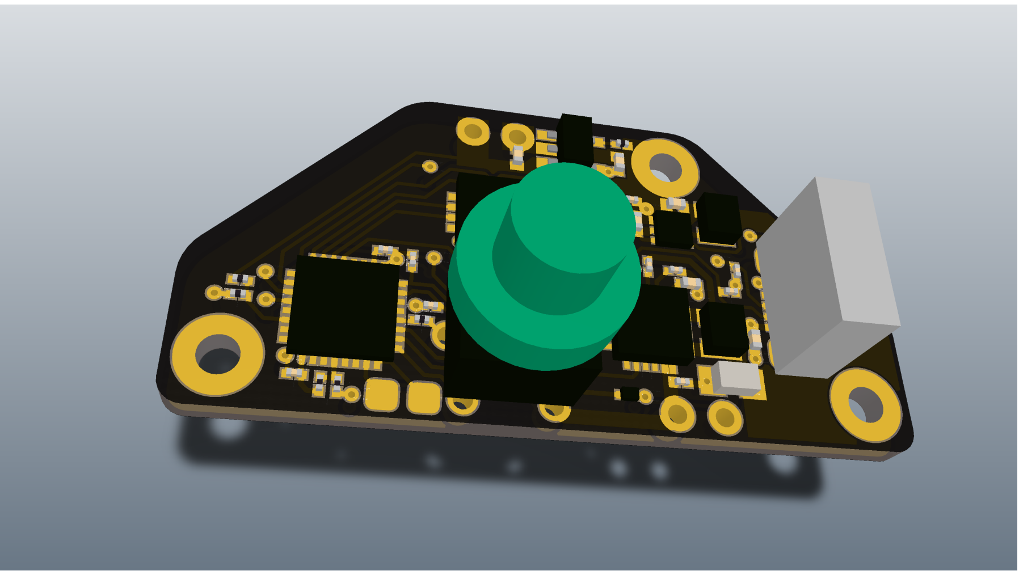
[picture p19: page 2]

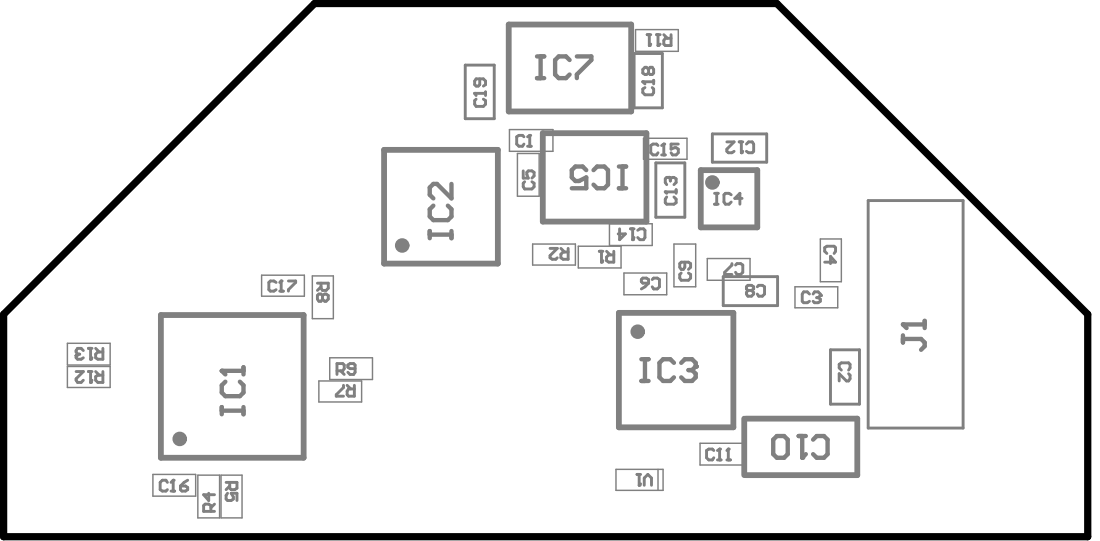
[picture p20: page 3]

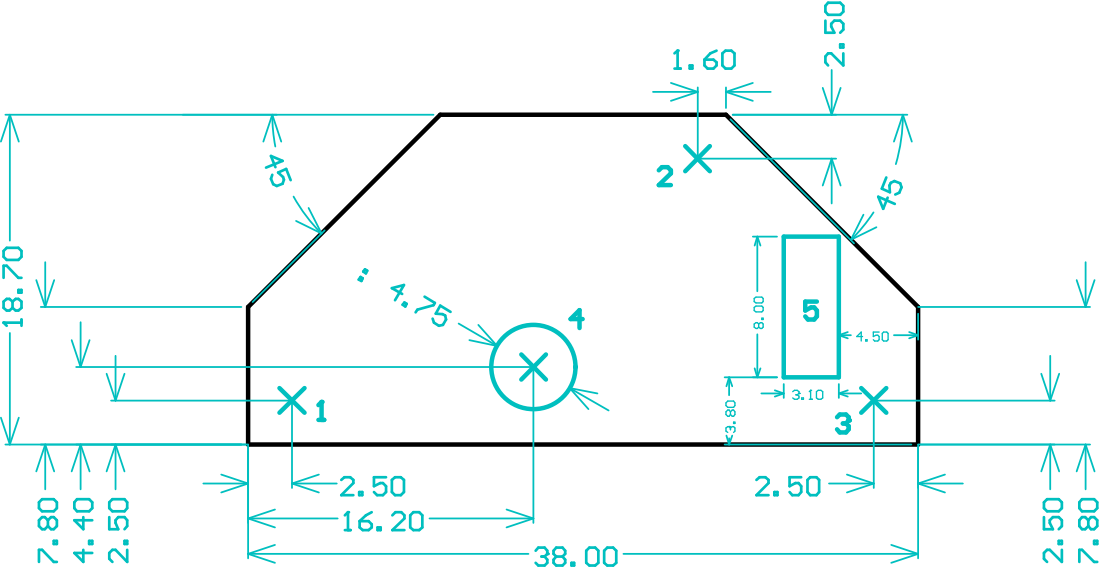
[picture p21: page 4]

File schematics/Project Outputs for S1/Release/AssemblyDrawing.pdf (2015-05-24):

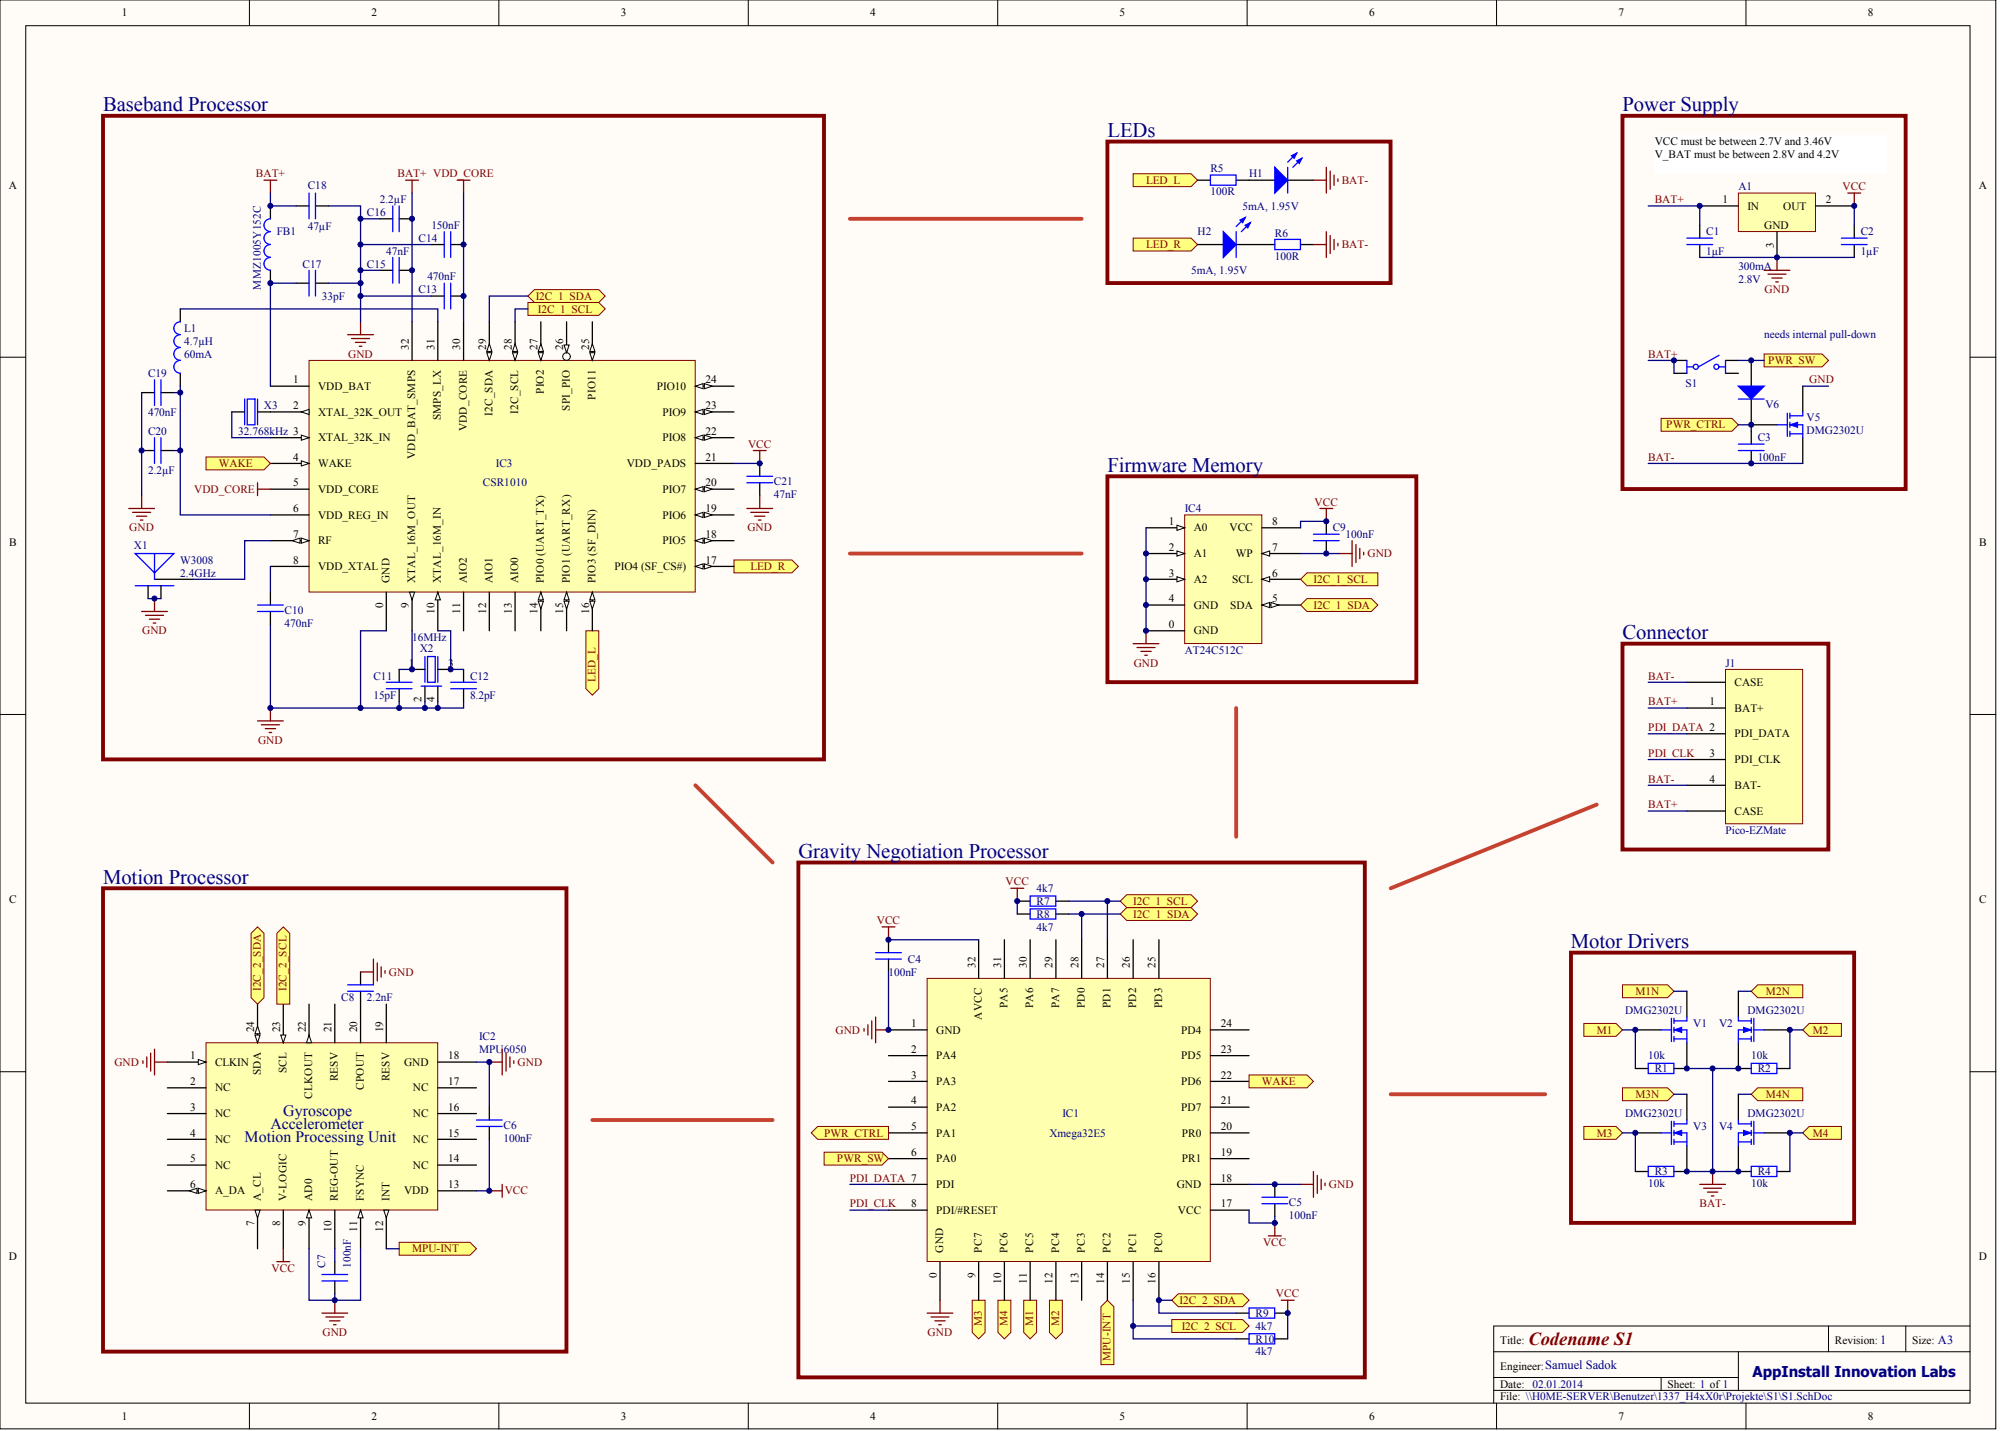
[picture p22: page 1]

VCC must be between 2.7V and 3.46V
V_BAT must be between 2.8V and 4.2V

needs internal pull-down

32.768kHz | 3

Codename S1 Title: | 1 Revision: | Size: A3

Engineer:Samuel Sadok | AppInstall Innovation Labs

Date: File:
\\H0ME-SERVER\Benutzer\1337_H4xX0r\Projekte\S1\S1.SchDoc

02.01.2014 | Sheet: 1 of 1

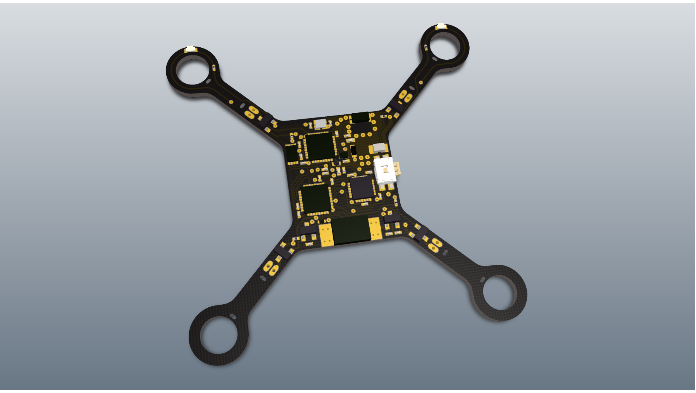
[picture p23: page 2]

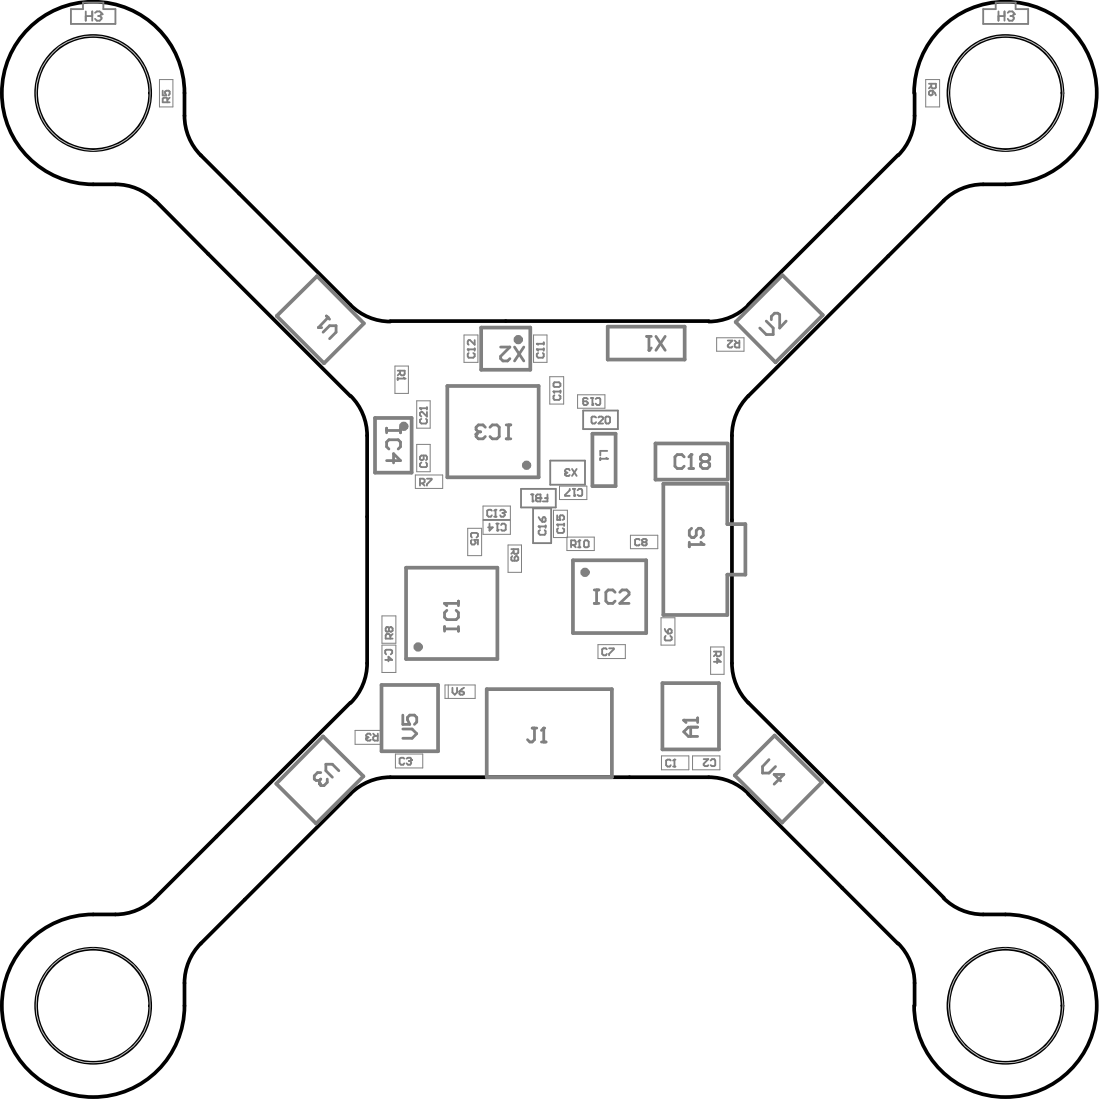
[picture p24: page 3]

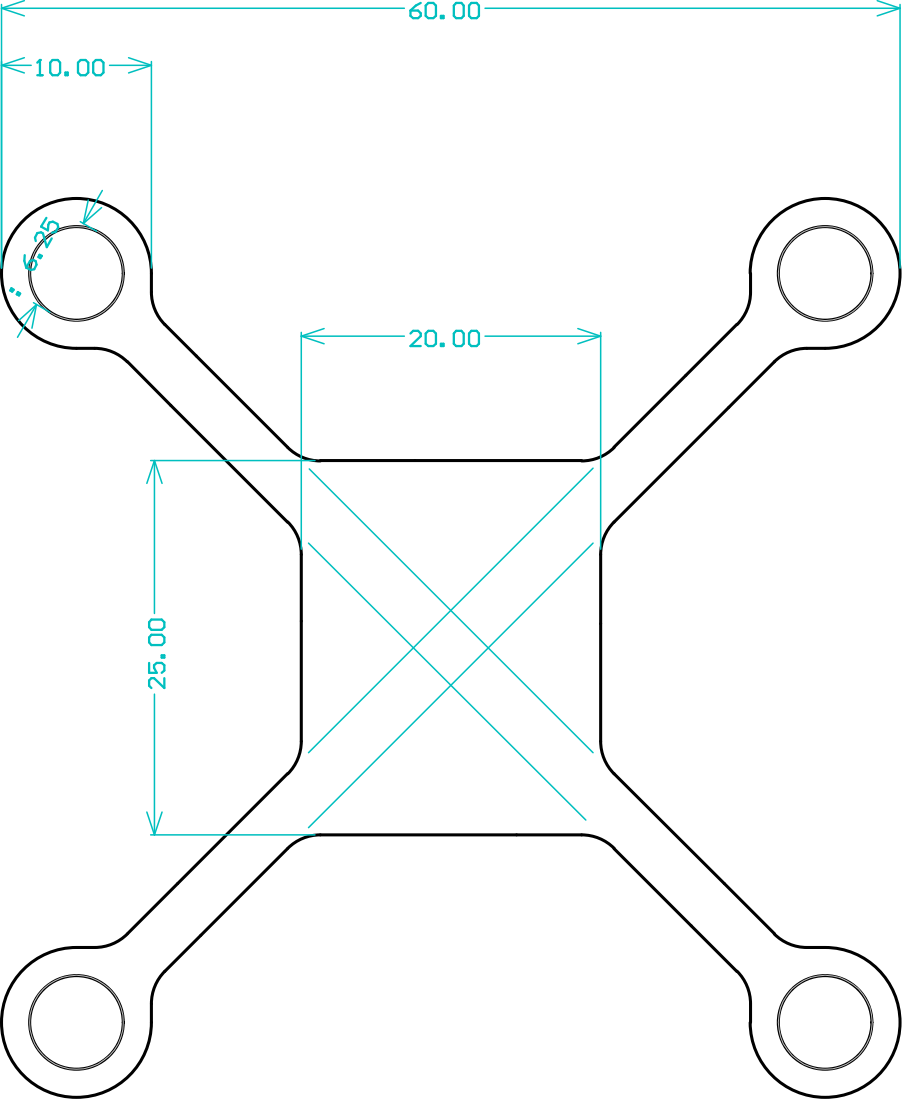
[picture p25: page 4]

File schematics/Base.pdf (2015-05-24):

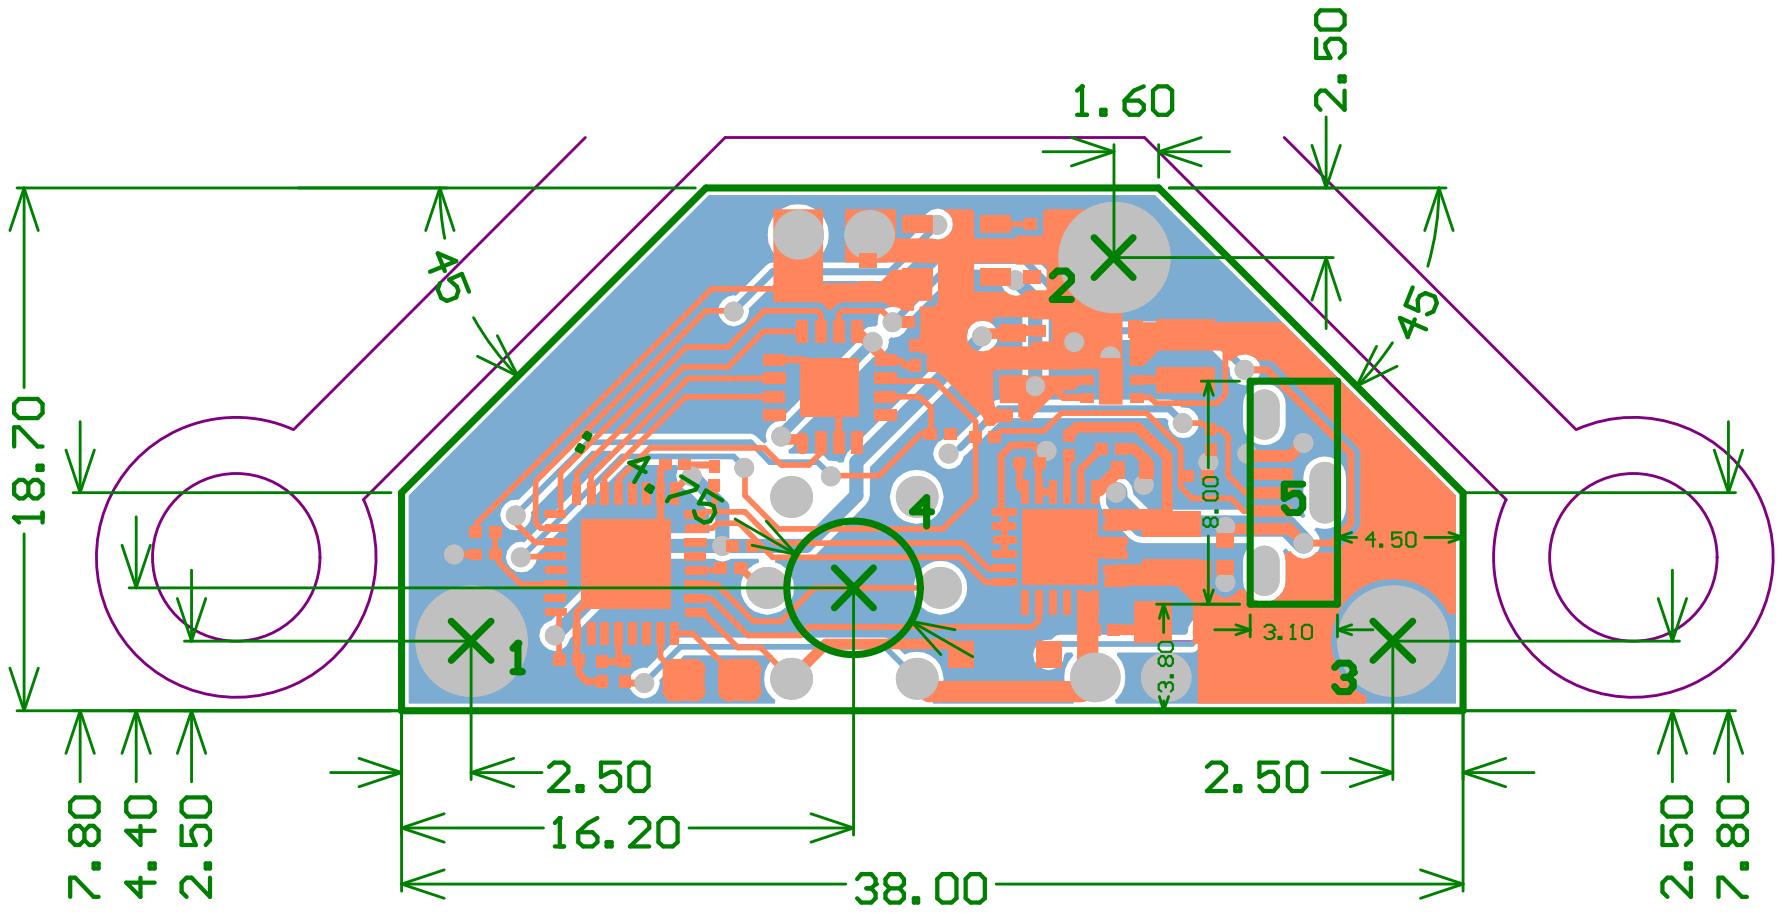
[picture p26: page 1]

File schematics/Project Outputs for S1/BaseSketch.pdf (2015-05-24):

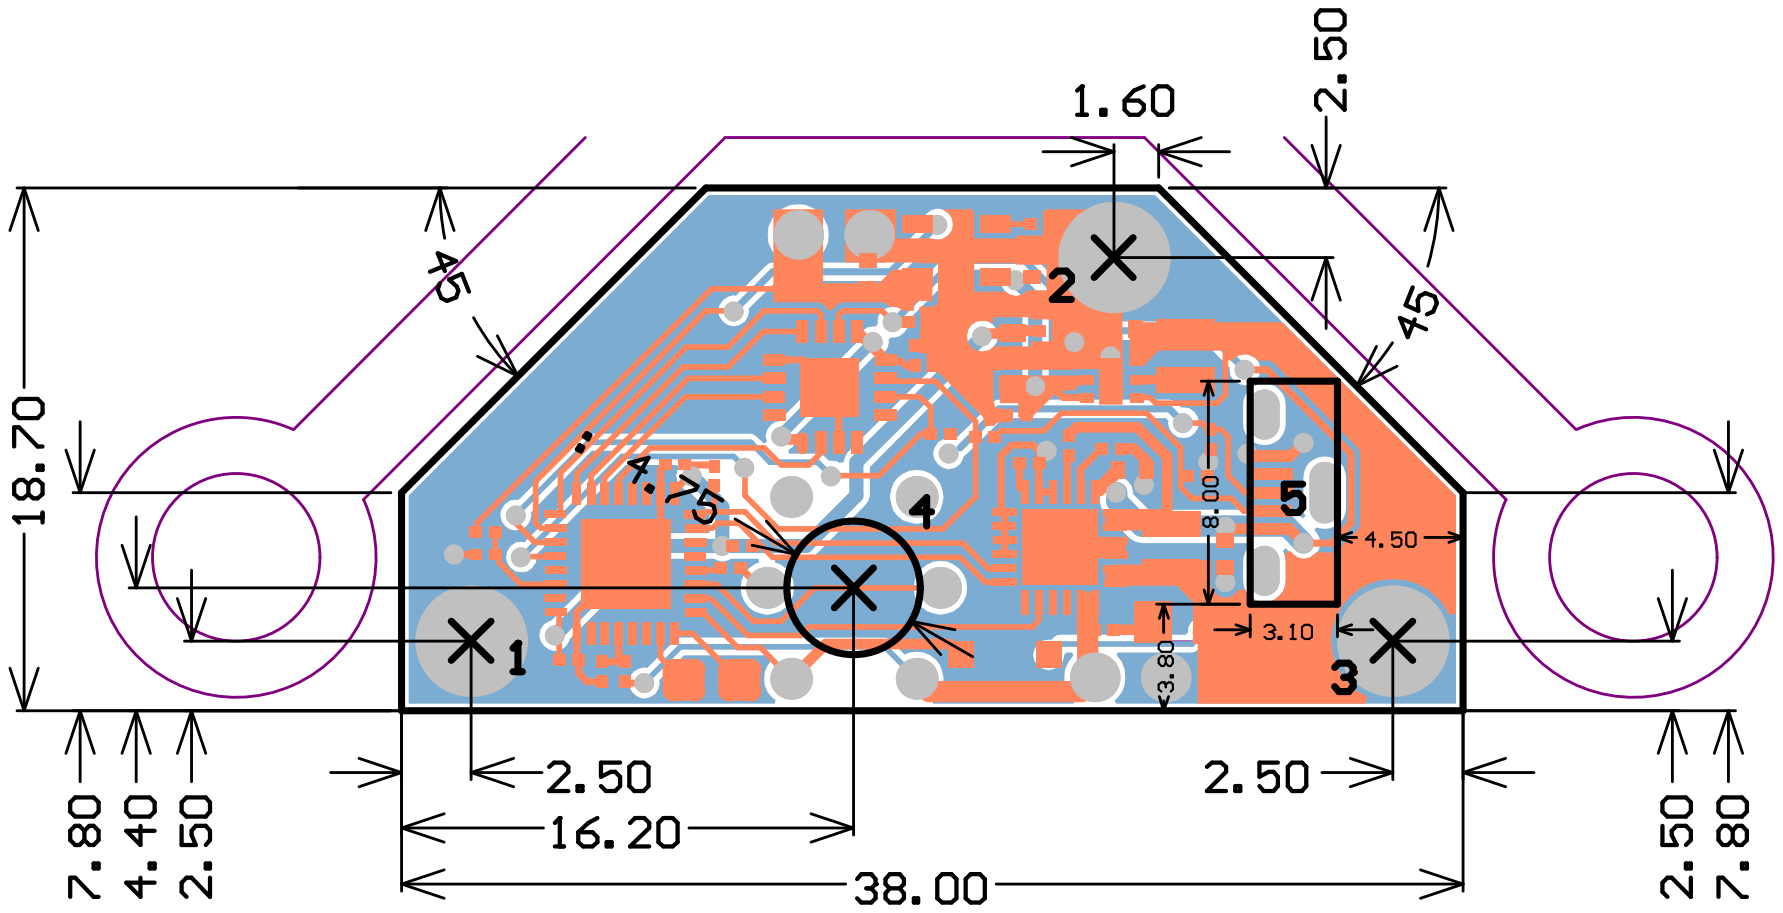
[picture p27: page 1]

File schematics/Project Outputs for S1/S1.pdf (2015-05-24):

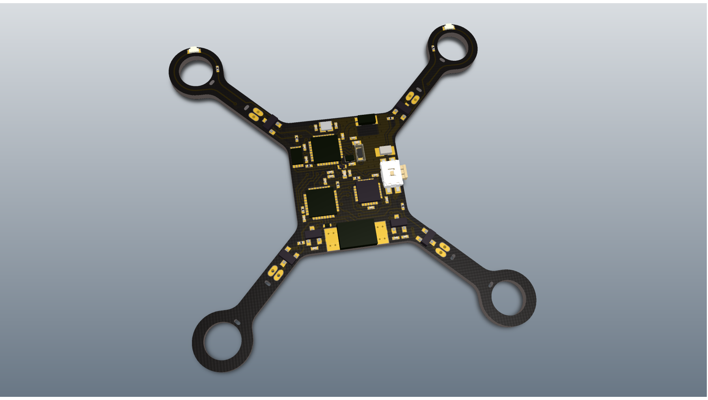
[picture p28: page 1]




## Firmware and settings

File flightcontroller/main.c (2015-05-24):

/*
 * GravityNegotiation.c
 *
 * Created: 07.03.2014 15:20:18
 *  Author: Samuel
 */ 

/*#include <system/system.h>
#include <baseband.h>
#include <system/math.h>*/
#include <system.h>
#include <uav/uav.h>


#define PITCH_LOG_SIZE	256


#define SAFETY_LIMIT 0x2000

/*



// Initializes power management
void pwr_init(void) {
	ioport_set_pin_level(GPIO_WAKE, 0);
	ioport_set_pin_mode(GPIO_WAKE, IOPORT_MODE_TOTEM);
	ioport_set_pin_dir(GPIO_WAKE, IOPORT_DIR_OUTPUT);
	
	//ioport_set_pin_level(GPIO_PWR_CTRL, 1); // as soon as the user releases the power button the gate capacitor starts discharging. We can keep it on by setting PWR_CTRL to high.
	//ioport_set_pin_dir(GPIO_PWR_CTRL, IOPORT_DIR_OUTPUT);
	//ioport_set_pin_mode(GPIO_PWR_CTRL, IOPORT_MODE_TOTEM);
	ioport_set_pin_mode(GPIO_PWR_SW, IOPORT_MODE_PULLDOWN);
	ioport_set_pin_dir(GPIO_PWR_SW, IOPORT_DIR_INPUT);
}

void pwr_wake_baseband(void) {
	ioport_set_pin_level(GPIO_WAKE, 1);
	_delay_ms(1);
	ioport_set_pin_level(GPIO_WAKE, 0);
}

// Shuts down the entire system down by opening the main power supply MOSFET.
// This routine does not return.
void pwr_shutdown(void) {
	ioport_set_pin_level(GPIO_PWR_CTRL, 1);
	while (1);
}


uint8_t pwr_needs_shutdown(void) {
	static uint8_t wasLow = 0;
	uint8_t power_switch = ioport_get_pin_level(GPIO_PWR_SW);
	if (!power_switch) wasLow = 1;
	return (wasLow && power_switch);
}

uint8_t pwr_switch_pressed(void) {
	static uint8_t state = 1;
	uint8_t lastState = state;
	state = ioport_get_pin_level(GPIO_PWR_SW);
	if (!lastState && state) {
		_delay_ms(50);
		return 1;
	}
	return 0;
}
*/


/*

typedef struct {
	uint16_t Version;
	struct {
		int16_t Throttle;
		math_ypr_t Attitude;
	} ControlInput;
	struct {
		math_kalman_t KalmanY;
		math_kalman_t KalmanP;
		math_kalman_t KalmanR;
		math_pid_t PidY;
		math_pid_t PidP;
		math_pid_t PidR;
	} Configuration;
	struct {
		math_ypr_t Attitude;
		math_ypr_t AngularRate;
	} PhysicalState;
	struct {
		uint16_t PitchLogCursor;
		int16_t PitchSensorLog[PITCH_LOG_SIZE];
		int16_t PitchActionLog[PITCH_LOG_SIZE];
	} DebugLog;
} register_file_t;


// the camera-estimated delay between input and output is around 150ms

register_file_t state = {
	.Version = 0x0001,
	.ControlInput = {
		.Throttle = 0,
		.Attitude = { .Yaw = 0, .Pitch = 0, .Roll = 0, .Flipped = 0 }
	},
	.Configuration = {
		.KalmanY = KALMAN_S,
		.KalmanP = KALMAN_S,
		.KalmanR = KALMAN_S,
		.PidY = CREATE_PID(0, 0, 0, 0),
		.PidP = PID_PR,
		.PidR = PID_PR
	},
	.DebugLog = {
		.PitchLogCursor = 0
	}
};


char *i2cRegisterFile = (char *)&state;
*/


int main(void)
{
	CREATE_ONBOARD_MPU();
	mpu_t mpu = ONBOARD_MPU;
	uav_t *uav = &localUAV;

	//_delay_ms(2000);
	io_init(); // initialize processor and built-in peripherals
	pwr_init(); // must be very early


	local_uav_set_mpu(&mpu);

	
	//_delay_ms(2000);
	//pwr_wake_baseband();
	//_delay_ms(2000);
	

	status_t status = STATUS_SUCCESS;
	LOGI("posA");
	if (!status) status = mpu_reset(&mpu);
	LOGI("posB");
	if (status) LOGE("err1");
	if (!status) status = mpu_start(&mpu);
	LOGI("posC");
	if (status) LOGE("err2");
	if (!status) status = uav_init(uav);
	LOGI("posD");
	if (status) LOGE("err3");
	if (!status) status = uav_on(uav);
	LOGI("posE");
	if (status) LOGE("err4");

	if (status != STATUS_SUCCESS) {
		LOGE("setup failed! %s, %d\n", "[todo: convert error code]", status);
		bug_check(status, 0);
	}
	
	LOGI("pos1");

	
	//tc45_write_cc(&TCC4, TC45_CCA, 320);
	//tc45_write_cc(&TCC4, TC45_CCB, 320);
	//tc45_write_cc(&TCC4, TC45_CCC, 320);
	//tc45_write_cc(&TCC4, TC45_CCD, 320);
	//tc45_enable_cc_channels(&TCC4, TC45_CCACOMP);
	//tc45_enable_cc_channels(&TCC4, TC45_CCBCOMP);
	//tc45_enable_cc_channels(&TCC4, TC45_CCCCOMP);
	//tc45_enable_cc_channels(&TCC4, TC45_CCDCOMP);
	//PORTC.REMAP |= 0x0F; // set PWM output pins
	
	//tc45_set_overflow_interrupt_level(&TCC5, TC45_INT_LVL_LO);

	uav_config_t config = {
		.reactivenessR = 30, .predictionTimeR = 50,
		.reactivenessP = 30, .predictionTimeP = 50,
		.PValP = 5, .IValP = 5, .DValP = 0, .maxIP = 2,
		.PValR = 5, .IValR = 5, .DValR = 0, .maxIR = 2
	};
	uav_config(uav, &config);
	
	float throttle = 0;
	uint8_t jumping = 1;
	for (;;) {
	    if (pwr_switch_pressed())
			jumping = !jumping;
		
		if (jumping) {
			//multirotor_set_motors(&device, 0x7FFF, 0, 0, 0);
			//_delay_ms(170);
			//multirotor_set_motors(&device, 0, 0x7FFF, 0, 0);
			////_delay_ms(30); // empty
			//_delay_ms(30);
			//
			//multirotor_set_motors(&device, 500, 0, 0, 0);
			//_delay_ms(2000);
			//multirotor_set_motors(&device, 0, 0, 0, 0);
			

			_delay_ms(1000);
			uav_control(uav, throttle = 0, NULL);
			for (size_t i = 0; i < 200; i++) {
				uav_control(uav, throttle += (1.0f / 200.0f), NULL);
				_delay_ms(5);
			}
			uav_control(uav, throttle = 0, NULL);
			//jumping = 0;
		}
	}
}



/*void __kernel_panic(uint16_t line, uint16_t error_code, uint16_t param1, uint16_t param2) {
	multirotor_init(&device);
	multirotor_on(&device);
	
	wdt_reset_mcu();
	while (1) {
		multirotor_set_motors(&device, 0x3FFF, 0, 0, 0);
		_delay_ms(10);
		multirotor_set_motors(&device, 0, 0, 0, 0);
		_delay_ms(1950);
	}
}*/

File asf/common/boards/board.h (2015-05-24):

/**
 * \file
 *
 * \brief Standard board header file.
 *
 * This file includes the appropriate board header file according to the
 * defined board (parameter BOARD).
 *
 * Copyright (c) 2009-2014 Atmel Corporation. All rights reserved.
 *
 * \asf_license_start
 *
 * \page License
 *
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
 * 3. The name of Atmel may not be used to endorse or promote products derived
 *    from this software without specific prior written permission.
 *
 * 4. This software may only be redistributed and used in connection with an
 *    Atmel microcontroller product.
 *
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
 * \asf_license_stop
 *
 */
 /**
 * Support and FAQ: visit <a href="http://www.atmel.com/design-support/">Atmel Support</a>
 */

#ifndef _BOARD_H_
#define _BOARD_H_

/**
 * \defgroup group_common_boards Generic board support
 *
 * The generic board support module includes board-specific definitions
 * and function prototypes, such as the board initialization function.
 *
 * \{
 */

#include "compiler.h"

#ifdef __cplusplus
extern "C" {
#endif


/*! \name Base Boards
 */
//! @{
#define EVK1100                     1  //!< AT32UC3A EVK1100 board.
#define EVK1101                     2  //!< AT32UC3B EVK1101 board.
#define UC3C_EK                     3  //!< AT32UC3C UC3C-EK board.
#define EVK1104                     4  //!< AT32UC3A3 EVK1104 board.
#define EVK1105                     5  //!< AT32UC3A EVK1105 board.
#define STK600_RCUC3L0              6  //!< STK600 RCUC3L0 board.
#define UC3L_EK                     7  //!< AT32UC3L-EK board.
#define XPLAIN                      8  //!< ATxmega128A1 Xplain board.
#define STK600_RC064X              10  //!< ATxmega256A3 STK600 board.
#define STK600_RC100X              11  //!< ATxmega128A1 STK600 board.
#define UC3_A3_XPLAINED            13  //!< ATUC3A3 UC3-A3 Xplained board.
#define UC3_L0_XPLAINED            15  //!< ATUC3L0 UC3-L0 Xplained board.
#define STK600_RCUC3D              16  //!< STK600 RCUC3D board.
#define STK600_RCUC3C0             17  //!< STK600 RCUC3C board.
#define XMEGA_B1_XPLAINED          18  //!< ATxmega128B1 Xplained board.
#define XMEGA_A1_XPLAINED          19  //!< ATxmega128A1 Xplain-A1 board.
#define XMEGA_A1U_XPLAINED_PRO     20  //!< ATxmega128A1U XMEGA-A1U Xplained Pro board.
#define STK600_RCUC3L4             21  //!< ATUCL4 STK600 board
#define UC3_L0_XPLAINED_BC         22  //!< ATUC3L0 UC3-L0 Xplained board controller board
#define MEGA1284P_XPLAINED_BC      23  //!< ATmega1284P-Xplained board controller board
#define STK600_RC044X              24  //!< STK600 with RC044X routing card board.
#define STK600_RCUC3B0             25  //!< STK600 RCUC3B0 board.
#define UC3_L0_QT600               26  //!< QT600 UC3L0 MCU board.
#define XMEGA_A3BU_XPLAINED        27  //!< ATxmega256A3BU Xplained board.
#define STK600_RC064X_LCDX         28  //!< XMEGAB3 STK600 RC064X LCDX board.
#define STK600_RC100X_LCDX         29  //!< XMEGAB1 STK600 RC100X LCDX board.
#define UC3B_BOARD_CONTROLLER      30  //!< AT32UC3B1 board controller for Atmel boards
#define RZ600                      31  //!< AT32UC3A RZ600 MCU board
#define SAM3S_EK                   32  //!< SAM3S-EK board.
#define SAM3U_EK                   33  //!< SAM3U-EK board.
#define SAM3X_EK                   34  //!< SAM3X-EK board.
#define SAM3N_EK                   35  //!< SAM3N-EK board.
#define SAM3S_EK2                  36  //!< SAM3S-EK2 board.
#define SAM4S_EK                   37  //!< SAM4S-EK board.
#define STK600_RCUC3A0             38  //!< STK600 RCUC3A0 board.
#define STK600_MEGA                39  //!< STK600 MEGA board.
#define MEGA_1284P_XPLAINED        40  //!< ATmega1284P Xplained board.
#define SAM4S_XPLAINED             41  //!< SAM4S Xplained board.
#define ATXMEGA128A1_QT600         42  //!< QT600 ATXMEGA128A1 MCU board.
#define ARDUINO_DUE_X              43  //!< Arduino Due/X board.
#define STK600_RCUC3L3             44  //!< ATUCL3 STK600 board
#define SAM4L_EK                   45  //!< SAM4L-EK board.
#define STK600_MEGA_RF             46  //!< STK600 MEGA RF EVK board.
#define XMEGA_C3_XPLAINED          47  //!< ATxmega384C3 Xplained board.
#define STK600_RC032X              48  //!< STK600 with RC032X routing card board.
#define SAM4S_EK2                  49  //!< SAM4S-EK2 board.
#define XMEGA_E5_XPLAINED          50  //!< ATxmega32E5 Xplained board.
#define SAM4E_EK                   51  //!< SAM4E-EK board.
#define ATMEGA256RFR2_XPLAINED_PRO 52  //!< ATmega256RFR2 Xplained Pro board.
#define SAM4S_XPLAINED_PRO         53  //!< SAM4S Xplained Pro board.
#define SAM4L_XPLAINED_PRO         54  //!< SAM4L Xplained Pro board.
#define ATMEGA256RFR2_ZIGBIT       55  //!< ATmega256RFR2 zigbit
#define XMEGA_RF233_ZIGBIT         56  //!< ATxmega256A3U with AT86RF233 Zigbit
#define XMEGA_RF212B_ZIGBIT        57  //!< ATxmega256A3U with AT86RF212B Zigbit
#define SAM4S_WPIR_RD              58  //!< SAM4S-WPIR-RD board.
#define SAMD20_XPLAINED_PRO        59  //!< SAM D20 Xplained Pro board
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

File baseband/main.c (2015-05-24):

#include <system.h>



int main(void) {

	// todo: init LEDs
	// todo: init comms with flight processor

	PioSetModes((1UL << PIO_LED_L) | (1UL << PIO_LED_R), pio_mode_user);
	PioSetDir(PIO_LED_L, TRUE);
	PioSetDir(PIO_LED_R, TRUE);
	PioSetPullModes((1UL << PIO_LED_L) | (1UL << PIO_LED_R),
					pio_mode_strong_pull_up);

	PioSet(PIO_LED_R, 1UL);
	PioSet(PIO_LED_L, 1UL);

	// todo: initialize profile specific data
	// todo: read configuration store (blah = CSReadUserKey(KEY_INDEX);)

	ble_start();

	return 0;
}

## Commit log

2015-05-24 improved windows abstraction layer and simulation endpoints in C framework
2015-05-25 moved new class to shared framework
2015-05-25 added RemoteControl and Simulator projects, started to incorporate framework changes into RemoteControl project
2015-05-25 Squashed 'shared-c#/' changes from 98a5d35..9e31dca
    9e31dca moved new class to shared framework
    git-subtree-dir: shared-c#
    git-subtree-split: 9e31dca5aec9d27cc81ff84936183a7ebac3ecaf
2015-05-25 SlowAction/DataSource: added soft trigger/refresh capability iOS Bluetooth: device discovery is now managed by a CollectionSource Application: UI now uses the common view controller framework
2015-08-15 started with android abstraction layer initial commit of usbmodule
    [20081114_pv_ledilstar_L_mechModel.stp, Battery.SchDoc, C&R.SchLib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]
2015-08-25 Squashed 'shared-c/' changes from d5a7624..5d6dbec
    5d6dbec improved windows abstraction layer and simulation endpoints in C framework
    git-subtree-dir: shared-c
    git-subtree-split: 5d6dbec50b4333661101b97fddd7ce5074af9634
